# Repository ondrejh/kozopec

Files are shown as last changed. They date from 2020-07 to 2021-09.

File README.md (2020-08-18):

msp430 based stepper driver logic
=================================

## Description

The device is using small mcu to generate pulses for stepper driver. It has 3 digital inputs (forward, backward and release), one analog input (speed) and 3 outputs (PUL, DIR, ENA). The speed (frequency of the pulses) follows ramps to make start and stop softer. If the release input is active, the motor is released (no current) when its stopped.

## Prototype and programmer

Insert image here ..

## Second prototype

Insert image here ..

TODO:
1) vyzkouset
2) doplnit dokumentaci

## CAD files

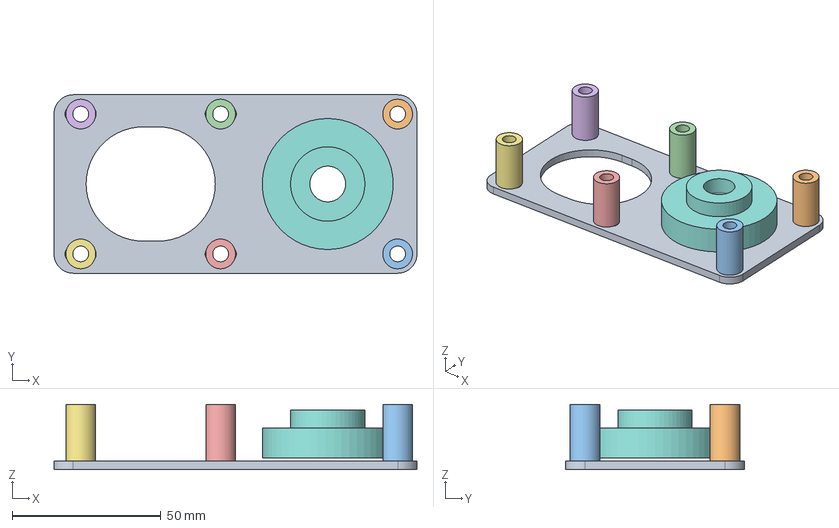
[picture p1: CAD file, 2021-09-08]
mech/holder_small.FCStd
122.0 x 60.0 x 22.0 mm

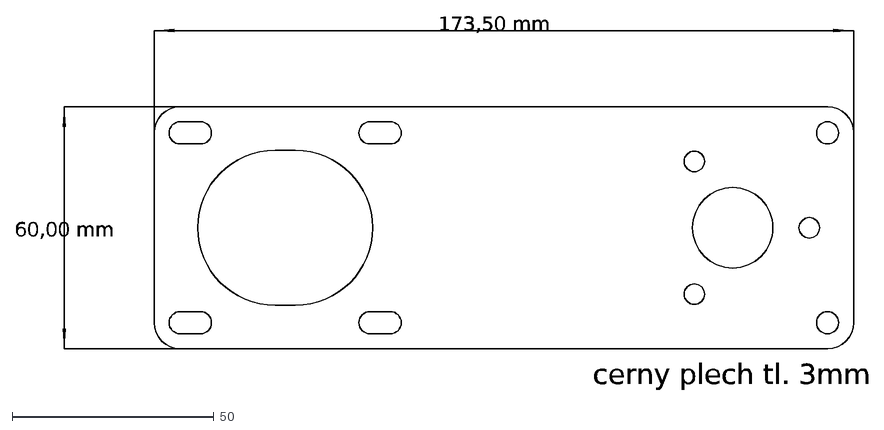
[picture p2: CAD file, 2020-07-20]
mech/sketch.dxf
173,50 mm
60,00 mm
cerny plech tl. 3mm

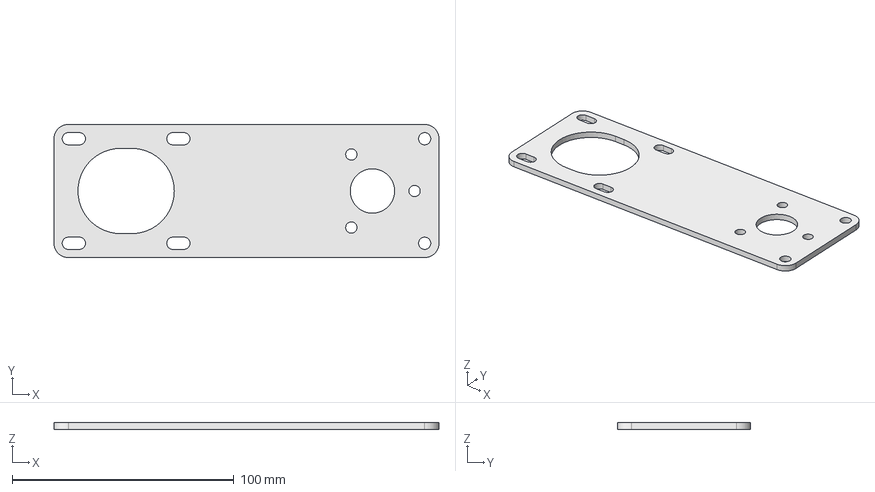
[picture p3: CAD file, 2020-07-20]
mech/holder.FCStd
173.5 x 60.0 x 3.00 mm

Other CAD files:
mech/holder_small.dxf

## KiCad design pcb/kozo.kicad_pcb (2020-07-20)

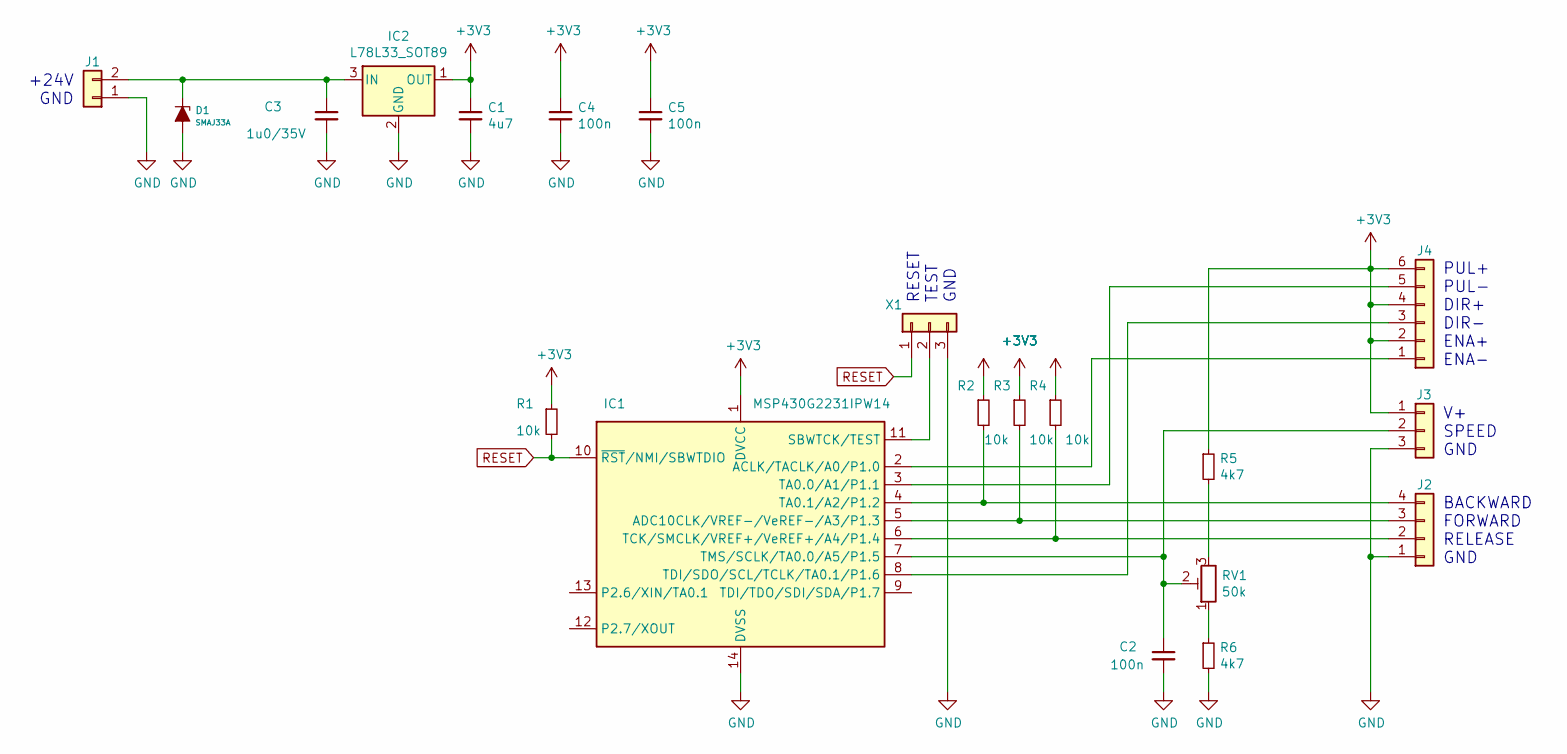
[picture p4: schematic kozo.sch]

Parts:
C1: 4u7; C_1206
C2, C4, C5: 100n; C_0603
C3: 1u0/35V; C_1206
D1: SMAJ33A; D_SMA
IC1: MSP430G2231IPW14; TSSOP-14_4.4x5mm_Pitch0.65mm
IC2: L78L33_SOT89; SOT-89-3
J1: Conn_01x02; PA257_508_02
J2: Conn_01x04; PA357_381_04
J3: Conn_01x03; Pin_Header_Straight_1x03_Pitch2.54mm
J4: Conn_01x06; PA257_508_06
R1, R2, R3, R4: 10k; R_0603
R5, R6: 4k7; R_0603
RV1: 50k; Potentiometer_Trimmer-EVM3E
X1: Conn_01x03; Pin_Header_Straight_1x03_Pitch2.54mm

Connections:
+3V3: C1.1, C4.1, C5.1, IC1.1 (DVCC), IC2.1 (OUT), J3.1, J4.2, J4.4, J4.6, R1.1, R2.1, R3.1, R4.1, R5.1
GND: C1.2, C2.2, C3.2, C4.2, C5.2, D1.2 (A), IC1.14 (DVSS), IC2.2 (GND), J1.1, J2.1, J3.3, R6.2, X1.3
unnamed: C2.1, IC1.7 (TMS/SCLK/TA0.0/A5/P1.5), J3.2, RV1.2
unnamed: C3.1, D1.1 (K), IC2.3 (IN), J1.2
unnamed: IC1.2 (ACLK/TACLK/A0/P1.0), J4.1
unnamed: IC1.3 (TA0.0/A1/P1.1), J4.5
unnamed: IC1.4 (TA0.1/A2/P1.2), J2.4, R2.2
unnamed: IC1.5 (ADC10CLK/VREF-/VeREF-/A3/P1.3), J2.3, R3.2
unnamed: IC1.6 (TCK/SMCLK/VREF+/VeREF+/A4/P1.4), J2.2, R4.2
unnamed: IC1.8 (TDI/SDO/SCL/TCLK/TA0.1/P1.6), J4.3
unnamed: IC1.11 (SBWTCK/TEST), X1.2
unnamed: R5.2, RV1.3
unnamed: R6.1, RV1.1
RESET: IC1.10 (~RST~/NMI/SBWTDIO), R1.2, X1.1

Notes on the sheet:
PUL+ PUL- DIR+ DIR- ENA+ ENA-
BACKWARD FORWARD RELEASE GND
V+ SPEED GND
RESET TEST GND
+24V GND

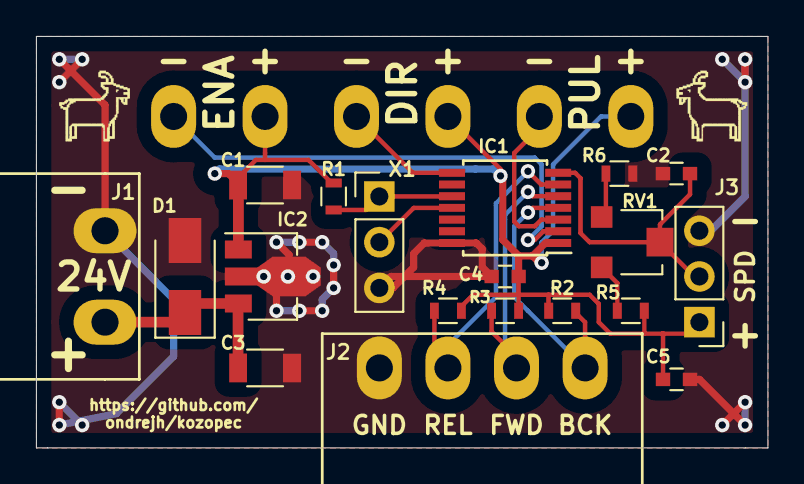
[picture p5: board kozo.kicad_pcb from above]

Board: 2 copper layers, 40.6 x 22.9 mm, 22 parts (1 on the bottom side), 14 nets.

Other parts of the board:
LOGO: koza
LOGO#2: koza_inv

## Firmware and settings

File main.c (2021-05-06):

//******************************************************************************
// Simple stepper driver with MSP430 mcu
//
//
// author:          Ondrej Hejda
// date (started):  26.6.2020
//
// hardware: MSP430G2553 / MSP430G2452
//
//                MSP4302553
//             -----------------
//         /|\|                 |
//          | |             P1.2|<---- BACKWARD
//          --|RST          P1.3|<---- FORWARD
//            |             P1.4|<---- RELEASE
//            |                 |
//            |             P1.5|<---- SPEED (analog 0 .. 3.3V)
//            |                 |
//            |             P1.0|----> ENABLE
//            |             P1.1|----> STEP
//            |             P1.6|----> DIRRECTION
//            |                 |
//
//******************************************************************************

// include section
//#include <msp430g2553.h>
//#include <msp430g2452.h>
//#include <msp430g2231.h>
#include <msp430.h>

#include <stdint.h>
#include <stdbool.h>

#define BTN_PUSH 100
#define BTN_HOLD 1000

// on-board leds
#define LED_INIT() do{P1DIR|=0x41;P1OUT&=~0x41;}while(0)
#define LED_RED_ON() do{P1OUT|=0x01;}while(0)
#define LED_RED_OFF() do{P1OUT&=~0x01;}while(0)
#define LED_RED_SWAP() do{P1OUT^=0x01;}while(0)
#define LED_GREEN_ON() do{P1OUT|=0x40;}while(0)
#define LED_GREEN_OFF() do{P1OUT&=~0x40;}while(0)
#define LED_GREEN_SWAP() do{P1OUT^=0x40;}while(0)

// on-board button
#define BUTTON_INIT() do{P1DIR&=~BIT3;P1REN|=BIT3;}while(0)
#define BUTTON ((P1IN&BIT3)==0)

// inputs (button with pull-up, active low)
#define INPUT_INIT() do{P1DIR&=~0x1C;P1REN|=0x1C;}while(0)
#define FORWARD ((P1IN&BIT3)==0)
#define BACKWARD ((P1IN&BIT2)==0)
#define RELEASE ((P1IN&BIT4)!=0)

// motor outputs (opto-coupled outputs, active low)
#define MOTOR_INIT() do{P1DIR|=0x43;P1OUT&=~43;}while(0)
#define MOTOR_DIR(x) do{(x)?(P1OUT|=BIT6):(P1OUT&=~BIT6);}while(0)
#define FORW 0
#define BACK 1
#define DIR_FORW ((P1OUT&BIT6)!=0)
#define DIR_BACK ((P1OUT&BIT6)==0)
#define MOTOR_STEP() do{P1OUT^=BIT1;}while(0)
#define MOTOR_ENABLE() do{P1OUT|=BIT0;}while(0)
#define MOTOR_DISABLE() do{P1OUT&=~BIT0;}while(0)
#define MOTOR_ENABLED ((P1OUT&BIT0)==0)

#define STEP_DIV 200 // 5000Hz / 1MHz
#define STEP_OVF 1500
#define STEP_ACC 5
#define MAX_SPEED 500

// leds and dco init
void board_init(void)
{
	// oscillator
	BCSCTL1 = CALBC1_1MHZ; // Set DCO
	DCOCTL = CALDCO_1MHZ;

    // button
    BUTTON_INIT();

    // leds
	LED_INIT();

	// motor
	MOTOR_INIT();

	// inputs
	INPUT_INIT();

	// analog input
	P1DIR &= ~BIT5; P1SEL |= BIT5;
	ADC10CTL1 = INCH_5 + ADC10DIV_3 ;         // Channel 3, ADC10CLK/3
	ADC10CTL0 = SREF_0 + ADC10SHT_3 + ADC10ON;
    //ADC10CTL0 = ADC10SHT_2 + ADC10ON; // ADC10ON, interrupt enabled
    //ADC10CTL1 = INCH_5;               // input A5
    ADC10AE0 |= BIT5;                 // PA.5 ADC option select
    ADC10CTL0 |= ENC + ADC10SC;       // start conversion

	// free running timer
	TACCR0 = 0xFFFF;
	TACTL = TASSEL_2 + MC_1; // SMCLK, upmode
}

// main program body
int main(void)
{
	WDTCTL = WDTPW + WDTHOLD;	// Stop WDT

	board_init(); // init hw

	enum {
	    MOD_STOP = 0,
	    MOD_FWD_PUSH,
	    MOD_FWD_HOLD,
	    MOD_BWD_PUSH,
	    MOD_BWD_HOLD,
	} mode = MOD_STOP;

	while(1) // main loop
	{
	    // motor step control
	    static uint16_t mt = 0;
	    static uint16_t mp = 0; // step period
	    static int16_t mv = 0; // step speed, if 0 stop
	    static int16_t ma = 0;
	    static int16_t max_speed = 200;
	    bool fwd_push = false, bwd_push = false;
	    static bool fwd_hold = false, bwd_hold = false, rel_hold = false;
        if ((TAR - mt) > STEP_DIV) {
            if (mv!=0) {
                mt += STEP_DIV;
                mp += mv;
                if (mp > STEP_OVF) {
                    mp -= STEP_OVF;
                    MOTOR_STEP();
                }
            }
            else {
                mt = TAR;
                mp = 0;
            }
            // speed control
            static int cnt = 0;
            if (cnt==10) {
                mv += ma;
                if (mv >= max_speed) mv = max_speed;
                if (mv < 0) mv = 0;
                cnt = 0;
            }
            cnt ++;

            static int adc_cnt = 0;
            if (adc_cnt >= 500) {
                adc_cnt = 0;
                max_speed = ADC10MEM + 200;
                ADC10CTL0 |= ENC + ADC10SC;
            }
            adc_cnt++;

    	    static uint16_t btn_fwd = 0, btn_bwd = 0, btn_rel = 0;
	        static bool fwd_stat = false, bwd_stat = false;

	        // button filtering
            if (FORWARD) {
                if (btn_fwd < BTN_HOLD) {
                    btn_fwd ++;
                    if (btn_fwd >= BTN_PUSH)
                        fwd_stat = true;
                } else
                    fwd_hold = true;
            } else {
                if (btn_fwd > BTN_PUSH) {
                    btn_fwd = BTN_PUSH;
                    if (fwd_stat == true)
                        fwd_push = true;
                } else if (btn_fwd > 0)
                    btn_fwd --;
                else {
                    fwd_stat = false;
                    fwd_hold = false;
                }
            }

            if (BACKWARD) {
                if (btn_bwd < BTN_HOLD) {
                    btn_bwd ++;
                    if (btn_bwd >= BTN_PUSH)
                        bwd_stat = true;
                } else
                    bwd_hold = true;
            } else {
                if (btn_bwd > BTN_PUSH) {
                    btn_bwd = BTN_PUSH;
                    if (bwd_stat == true)
                        bwd_push = true;
                } else if (btn_bwd > 0)
                    btn_bwd --;
                else {
                    bwd_stat = false;
                    bwd_hold = false;
                }
            }

            if (RELEASE) {
                if (btn_rel < BTN_PUSH)
                    btn_rel ++;
                else
                    rel_hold = true;
            } else {
                if (btn_rel > 0)
                    btn_rel --;
                else
                    rel_hold = false;
            }
	    }

	    // system sequential
        static int seqv = 0;
        switch (seqv) {
        case 0: // wait button
            mode = MOD_STOP;
            if (fwd_push)
                mode = MOD_FWD_PUSH;
            if (bwd_push)
                mode = MOD_BWD_PUSH;
            if (fwd_hold)
                mode = MOD_FWD_HOLD;
            if (bwd_hold)
                mode = MOD_BWD_HOLD;

            if (mode != MOD_STOP) {
                if ((mode == MOD_FWD_PUSH) || (mode == MOD_FWD_HOLD))
                    MOTOR_DIR(1);
                else
                    MOTOR_DIR(0);
                MOTOR_ENABLE();
                mv = 0;
                ma = STEP_ACC;
                seqv++;
            }
            else {
                if (rel_hold)
                    MOTOR_DISABLE();
                else
                    MOTOR_ENABLE();
            }
            break;
        case 1: // acceleration, wait stop event (depends on mode)
            if ((((mode == MOD_FWD_PUSH) || (mode == MOD_BWD_PUSH)) && (fwd_push || bwd_push))
                || ((mode == MOD_FWD_HOLD) && (!fwd_hold))
                || ((mode == MOD_BWD_HOLD) && (!bwd_hold))) {
                ma = -STEP_ACC;
                seqv++;
            }
            break;
        case 2: // deceleration
            if (mv <= 0) {
                mv = 0;
                ma = 0;
                seqv = 0;
            }
            break;
        }
	}

	return -1;
}

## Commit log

2014-03-03 pwm dimming
2014-03-03 debug pwm, some blinking artwork
2014-03-09 button works
2020-06-26 forwar, backward, release button and some docu
2020-07-01 holder scatch
    [holder.FCStd]
2020-07-02 holder drawing
    [holder.FCStd, sketch.dxf]
2020-07-08 basic layout
    [kozo.kicad_pcb, kozo.sch]
2020-07-10 nice schmatic
    [kozo.kicad_pcb, kozo.sch]
2020-07-10 silk goat
    [kozo.kicad_pcb]
2020-07-10 mask debug
    [kozo.kicad_pcb]
2020-07-10 gerber data
    [kozo-B_Cu.gbr, kozo-B_Mask.gbr, kozo-Edge_Cuts.gbr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]
2020-07-10 pcb folder renamed
    [kozo.kicad_pcb, kozo.sch]
2020-07-21 push button mode
2021-05-06 gerber data archive
2021-09-08 small holder for smaler motor
    [holder_small.FCStd, holder_small.dxf]
2021-09-08 more parts
    [holder_small.FCStd]
